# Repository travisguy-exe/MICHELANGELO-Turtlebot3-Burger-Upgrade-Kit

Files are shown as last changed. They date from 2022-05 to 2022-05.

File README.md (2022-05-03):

# MICHELANGLEO - Turtlebot3 (Burger) Upgrade Kit

**A 3D printable, open-source upgrade kit for the Turtlebot3 Burger from Robotis.**

 <span xmlns:dct="http://purl.org/dc/terms/" property="dct:title">The</span> <a xmlns:cc="http://creativecommons.org/ns#" href="https://github.com/travisguy-exe/MICHELANGELO-Turtlebot3-Burger-Upgrade-Kit" property="cc:attributionName" rel="cc:attributionURL">MICHELANGELO - Turtlebot3 Burger Upgrade Kit</a> by Travis Guy is licensed under a <a rel="license" href="http://creativecommons.org/licenses/by-nc-sa/4.0/">Creative Commons Attribution-NonCommercial-ShareAlike 4.0 International License</a>.

## **Kit Overview**

The Michelangelo upgrade kit is intended to increase the overall modularity and usability of the Turtlebot3 Burger platform. This is a valuable upgrade for anyone looking to improve the physical user friendliness, durability and modularity of their Turtlebot3 Burger unit. The following list outlines the key features of the Michelangelo Kit.



####  **Kit Features:**

- **Enclosures:** Fully 3D printable enclosures for both the Burger's **Raspberry Pi** and **OpenCR** boards, with solid mounting points.
- **Multi-Generation Support:** The MICHEALANGELO kit supports both the  Raspberry Pi 3B+ and the Raspberry Pi 4 versions of the Turtlebot3 Burger. This project repository contains unique Raspberry Pi enclosure models for both versions of the Burger.  
- **Solid LIDAR Mount:** A 3D printable solid mount for the LDS-01 LIDAR unit.
- **Improved User Experience**: The MICHELANGELO kit reimagines the construction of the Turtlebot3 burger making it easier to access key ports on the system's control boards. At the same time the  kit's reconstruction makes the robot easier to disassemble and customize.
- **Improved Modularity:** The MICHELANGELO upgrade kit adds modular enclosures and mounts to all of the key components of the Turtlbot3 Burger. This allows each of these components to easily be relocated, swapped out or customized as the user see's fit. CAD documentation for all models are included in this repository to allow users to create their own custom variants depending on their needs.

## **Repository Overview**

This repository contains all of the files and instructions necessary to upgrade a standard Turtlebot3 Burger unit with the MICHELANGELO kit. It as well contains all of the CAD documentation that one would require to add their own features to this upgrade kit. The following list provides detail on each of the sub-folders within this directory and where to locate relevant information within them.

**Repository Folders:**

- **3D Printing Files:** This folder contains all of the necessary **STL** files for printing the upgrade kit's parts, as well as, instruction for post processing.

- **CAD Files:** Contained within this folder are the **Fusion 360** and **.step** solid models for the MICHELANGELO Kit assembly and its sub-assemblies.

------

## **Project Log**

The MICHELANGELO project is still under active development, which means features will be added to this repository as time goes on! Refer back to this log to see what is upcoming and what I have added!

### Work In Progress.

- Youtube Assembly/Overview Video

### Completed Work

2022/04/30 - Project Inception

	- CAD Files - MICHELANGELO v44 Master Assemblies
	- Assembly Documentation
	- STL Files/3D Printing Documentation

------

## Bill of Materials

The following table outlines the items required to complete the MICHELANGELO upgrade:

| Item/Description | Qty. | |
| :--- | :---: | :---: |
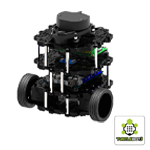
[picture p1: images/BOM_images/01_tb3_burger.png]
| Turtlebot 3 Burger Kit | 1 |   |
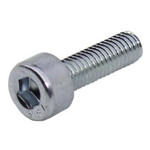
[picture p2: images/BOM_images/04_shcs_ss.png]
| **M3-0.5 x 6mm** - Socket Head Cap Screw - (42 Max.) | 12 (Min.) |  |
| **M3-0.5 x 16mm** - Socket Head Cap Screw | 12 |  |
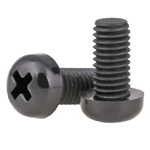
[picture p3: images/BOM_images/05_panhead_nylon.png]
| **M3-0.5 x 6mm** - Pan Head Screw (NYLON) | 8 |  |
| **M3-0.5 x 12mm** - Pan Head Screw (NYLON) | 2 |  |

# **Assembly Instructions**

	This section outlines the assembly instructions for the MICHELANGELO Upgrade Kit. These instructions assume that you have purchased all items in the **Bill of Materials** section and have 3D printed all relevant upgrade parts in accordance with the instructions laid out in the readme of the **3D Printing Files** folder.

------

### Step 1: TB3 Burger First Layer Assembly

------

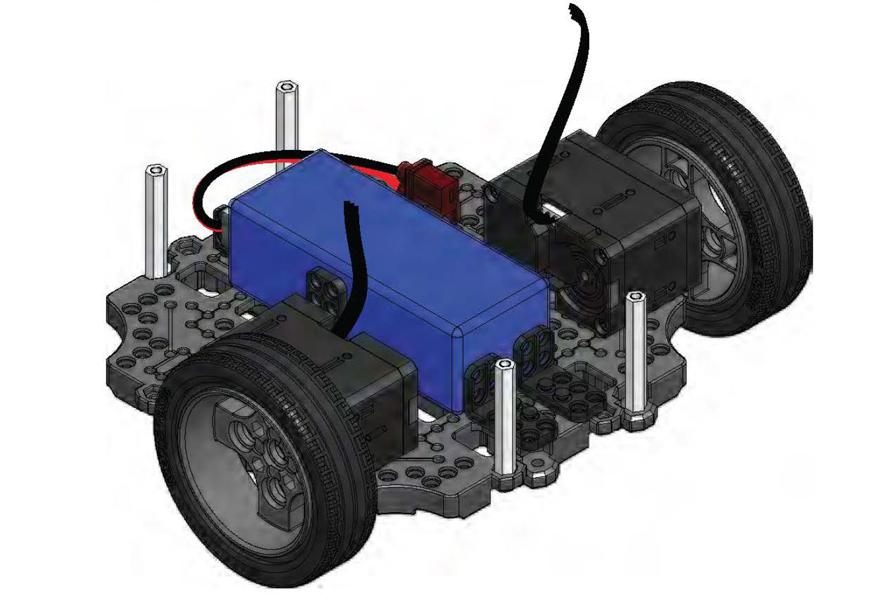
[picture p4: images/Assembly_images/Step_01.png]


The MICHELANGELO upgrade kit uses the **"First Layer Assembly"** from the standard Turtlebot3 Burger kit. Specific instructions for assembling the **"First Layer Assembly"** can be found on **Pages 11-15** of the Robotis Turtlebot3 Burger Assembly Manual. Once assembled, the **First Layer Assembly** can be set aside until **Step 4**

**Robotis Assembly Manual (Direct Download):** https://www.robotis.com/service/download.php?no=748

------

### Step 2: TB3 Burger Waffle Plate Assembly (x3)

------

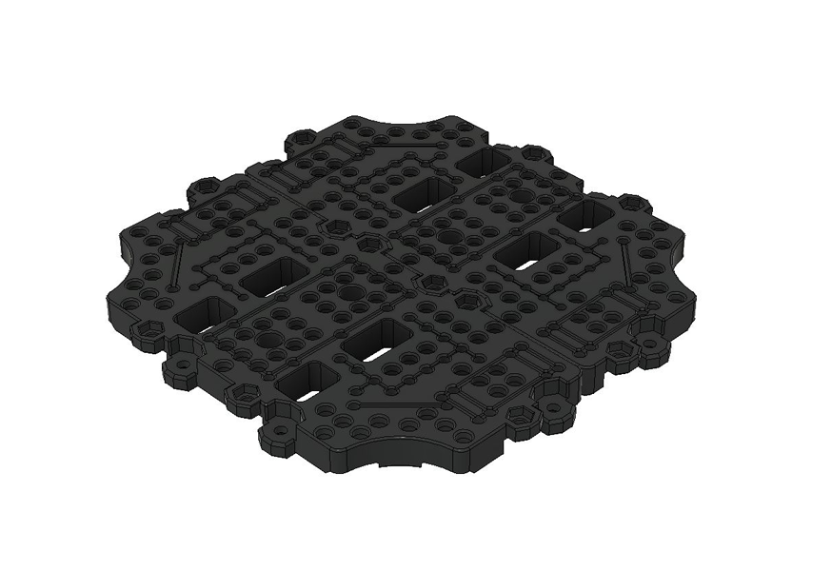
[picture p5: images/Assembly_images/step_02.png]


The MICHELANGELO kit uses the standard Burger waffle-plate assembly for all layers of the build. **Three** additional waffle-plates can be assembled at this point using the standard hardware from the Burger kit. These assembled waffle-plates can be set aside for later use in **Steps 3, 9 and 14**.

Instructions on **"Waffle-Plate Assembly"** can be found on **Page 9** of the Robotis Turtlebot3 Burger Assembly Manual. 

------

### Step 3: Second Layer Tap Locations ( OpenCR Enclosure Mounting)

------

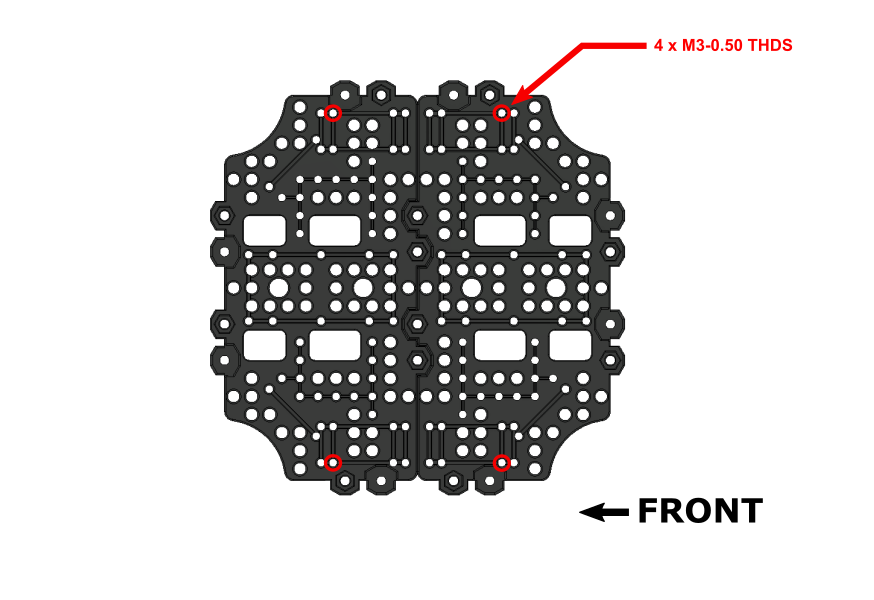
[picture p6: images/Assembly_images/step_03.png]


In order to attach the OpenCR board enclosure to a waffle-plate assembly, **4 pre-existing** holes must be modified. The image above indicates the relevant hole locations for tapping, an **M3-0.5** tap is required for this process. 

**NOTE:** Orientation of the second layer waffle-plate matters from this step onwards. Be sure to follow the orientation indicators for each subsequent step.

------

### Step 4: Second Layer Standoffs + OpenCR (Lower Enclosure) Installation

------

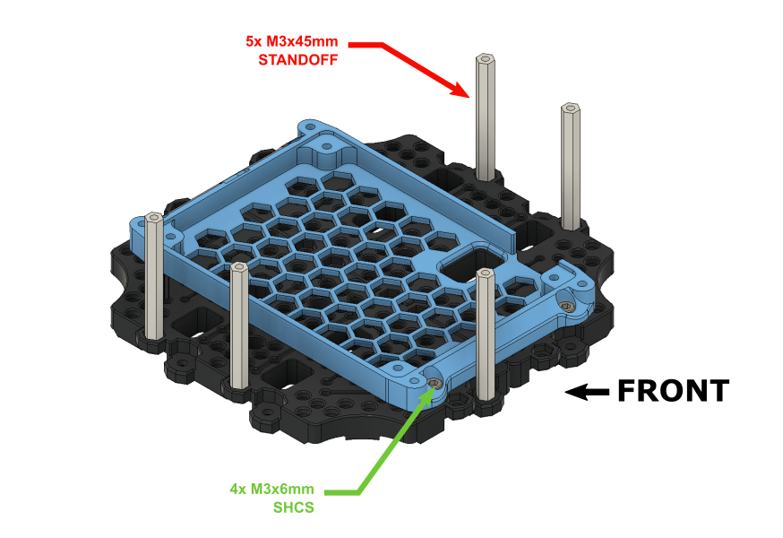
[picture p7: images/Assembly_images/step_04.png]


Attach the **OpenCR Lower Enclosure Half** to the **Second Layer Assembly** using **4 - M3x6mm Socket Screws**. Once the lower enclosure half is secured, install **5 - M3x45mm Standoffs** at the locations shown in the assembly image above. The standoffs can be attached with the standard **M3x8mm Philips** hardware from the Turtlbot3 Burger kit or an additional  **5 - M3x6mm Socket Screws**. 

------

### Step 5: Second Layer Attachment + Cable Routing

------

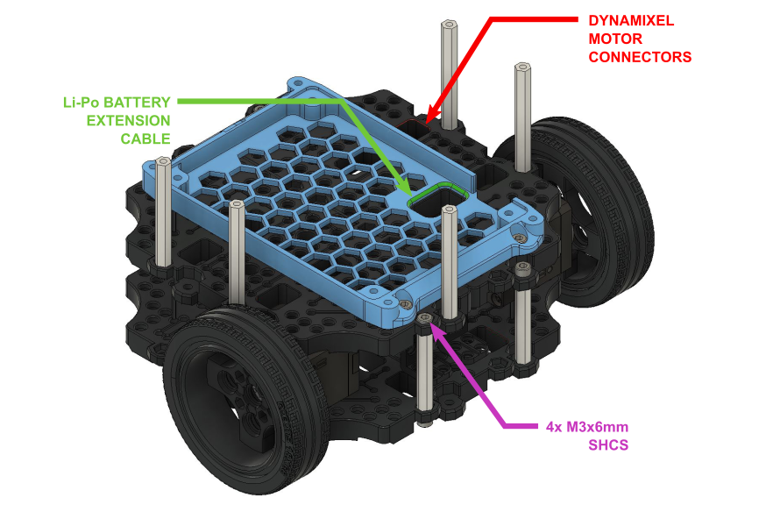
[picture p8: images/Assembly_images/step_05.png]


At this stage the **Second Layer Assembly** can be attached to the **First Layer Assembly** created in **Step 1**. However, before attachment, the **Dynamixel Motor Cables** and the **Li-Po Battery Extension Cable** from the first layer must be routed through the **Second Layer Assembly**. The image above shows the respective routing locations for each of the cables. 

A total of **4 - M3x6mm Socket Screws** screws are required to attach the second layer to the first. Alternatively, the standard **M3x8mm Philips**  hardware from the Turtlebot3 burger kit can be used in place of the socket screws. 

------

### Step 6: OpenCR Board Installation 

------

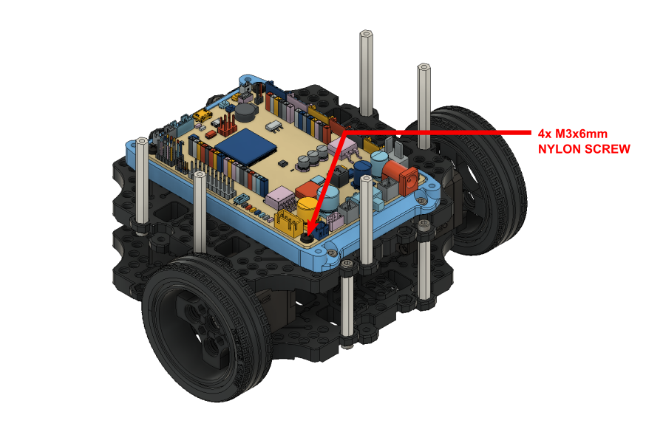
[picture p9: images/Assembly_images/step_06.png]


The **OpenCR** board  can now be installed into its lower enclosure half using **4 - M3x6mm Nylon Screws**. 

------

### Step 7: OpenCR Board Connections

------

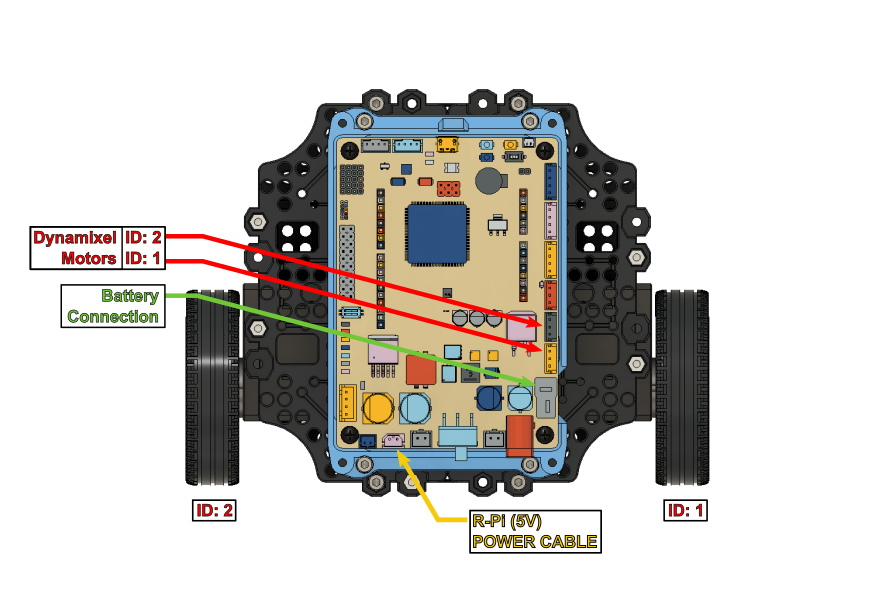
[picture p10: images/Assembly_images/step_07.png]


Before the OpenCR board can be fully enclosed a few electrical connections must be made: 

- [ ] Attach the **Dynamixel Motor** and **Li-Po Battery Extension** cables that were routed during **Step 5** to the OpenCR board. The connection points are indicated by the **RED** and **GREEN** arrowed text in the image above. 

  **NOTE:** Ensure correct connection of the Dynamixel motors by following the motor ID legend in the **RED** arrowed text. The motor IDs are indicated below each wheel for quick reference.

- [ ] Connect the **R-Pi (5v) Power Cable** to the OpenCR board at the point indicated by the **YELLOW** arrowed text in the image above. Leave this cable loose for routing in a later step.

------

### Step 8: OpenCR Enclosure Assembly

------

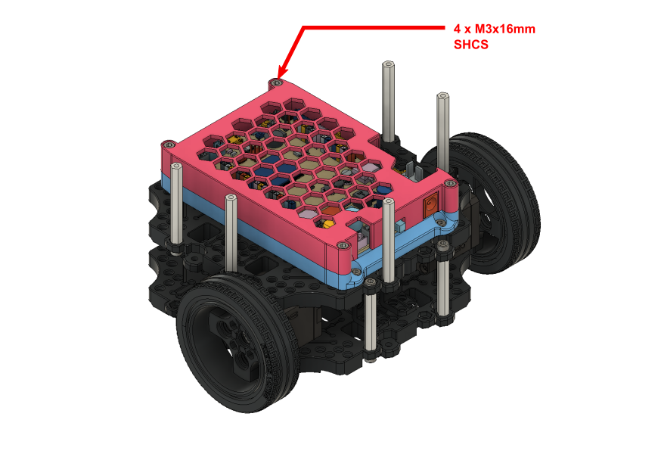
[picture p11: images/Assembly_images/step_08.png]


The OpenCR board can now be fully enclosed with it's upper enclosure half. As indicated in the assembly image above, a total of **4 - M3x16mm** fasteners will be required for this step.

------

### Step 9:  Third Layer Tap Locations (Raspberry Pi Enclosure Mounting)

------

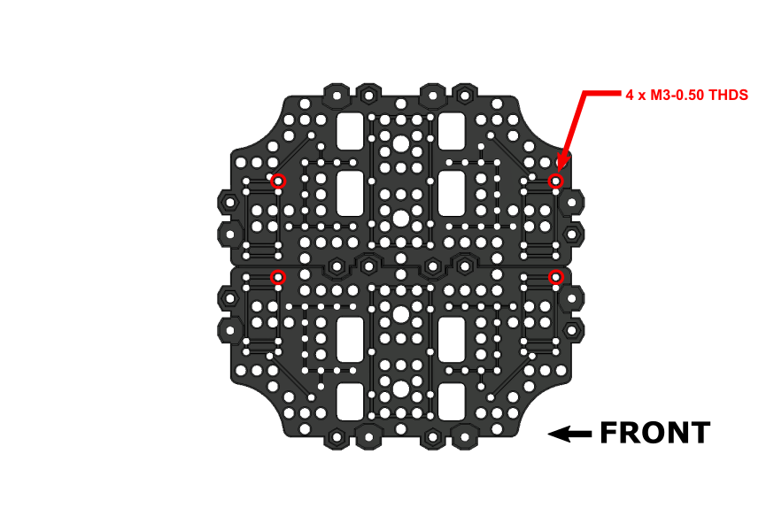
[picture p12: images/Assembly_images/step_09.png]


Whether you are using a **Raspberry Pi 3B+** or a **Raspberry Pi 4** the mounting footprint of theses enclosures in the MICHELANGELO upgrade kit are identical. These instructions apply for both models of the Turtlebot3 Burger.

In order to attach either Raspberry Pi board enclosure, **4 pre-existing** holes must be modified on the third layer waffle-plate. The **Step 3** image above indicates the relevant hole locations for tapping, an **M3-0.5** tap is required for this process. 

**NOTE:** Orientation of the third layer waffle-plate matters from this step onwards. Be sure to follow the orientation indicators for each subsequent step.

------

### Step 10:  Third Layer Standoffs + Raspberry Pi (Lower Enclosure) Installation

------

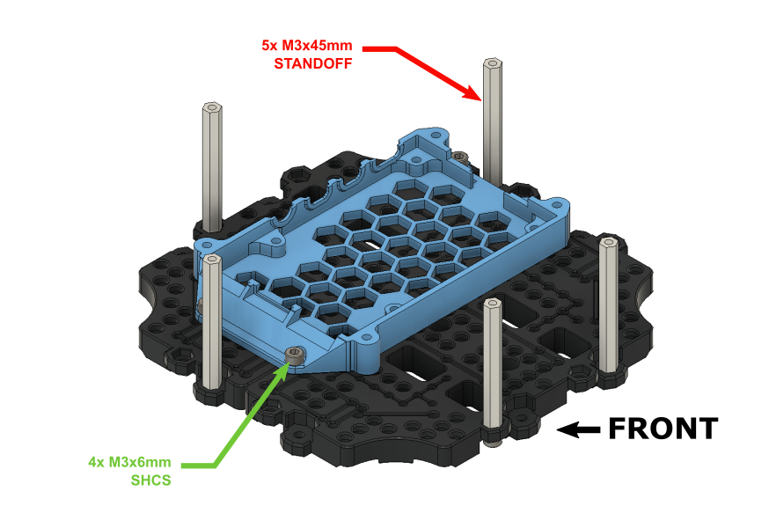
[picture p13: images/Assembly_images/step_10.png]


The **Raspberry Pi Lower Enclosure Half** can now be attached to the **Third Layer Assembly** using **4 - M3x6mm Socket Screws**. Once the lower enclosure half is secured, install **5 - M3x45mm Standoffs** at the locations shown in the assembly image above. The standoffs can be attached with the standard **M3x8mm Philips** hardware from the Turtlbot3 Burger kit or an additional  **5 - M3x6mm SHCS**. 

**NOTE:** This guide depicts the installation of the **Raspberry Pi 4** board. Instructions for the **Raspberry Pi 3B+** board are identical except for the usage of the relevant **3B+** enclosure pieces.

------

### Step 11:  Third Layer Attachment + Raspberry Pi Installation/Cable Routing

------

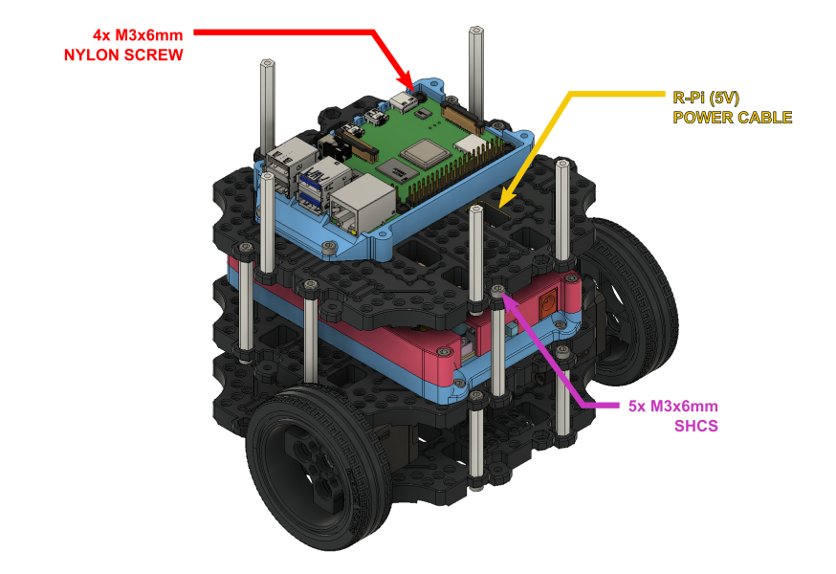
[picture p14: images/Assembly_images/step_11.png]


The **Third Layer Assembly** can now be attached to the main burger assembly using **5 - M3x6mm Socket Screws ** or the standard **M3x8mm Philips** hardware from the Burger kit. It is important that before fastening down the **Third Layer Assembly**, you first route the **R-Pi (5v) Power Cable** from **Step 7** up through the hole indicated by the **Yellow** arrowed text in the image above . 

Once the **Third Layer Assembly** is secured, install your Raspberry Pi unit into its mounted lower enclosure half using **4 - M3x6mm Nylon Screws**.

**NOTE:** Do not connect the **R-Pi (5v) Power Cable** during this step.

------

### Step 12:  Raspberry Pi Enclosure Assembly + Power Connection

------

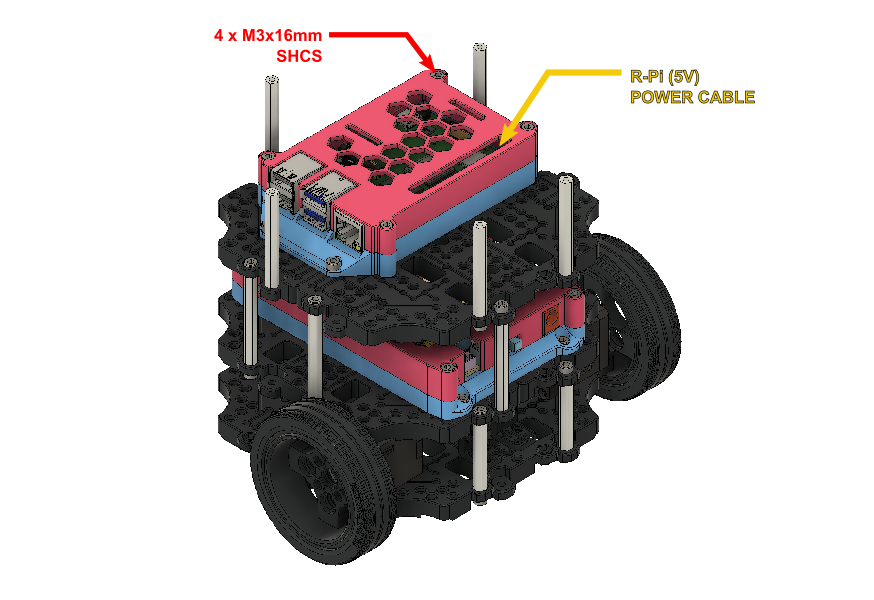
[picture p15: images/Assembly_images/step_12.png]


The Raspberry Pi board can now be fully enclosed with it's upper enclosure half, this step requires **4 - M3x16mm SHCS**.

Once the enclosure is assembled, connect the **R-Pi (5v) Power Cable** that was routed during **Step 11** to the Raspberry Pi unit.

**NOTE:** When connecting the power cable to the Raspberry Pi it is important to connect to the correct GPIO pins. Ensure that the **Positive** lead connects to **Pin 4** and the **Negative** lead connects to **Pin 6**. 

(Refer to **Page 22** of the Turtlebot3 Burger Assembly Manual for connection information.)

------

### Step 13:  Raspberry Pi - OpenCR USB Connection & Cable Routing

------

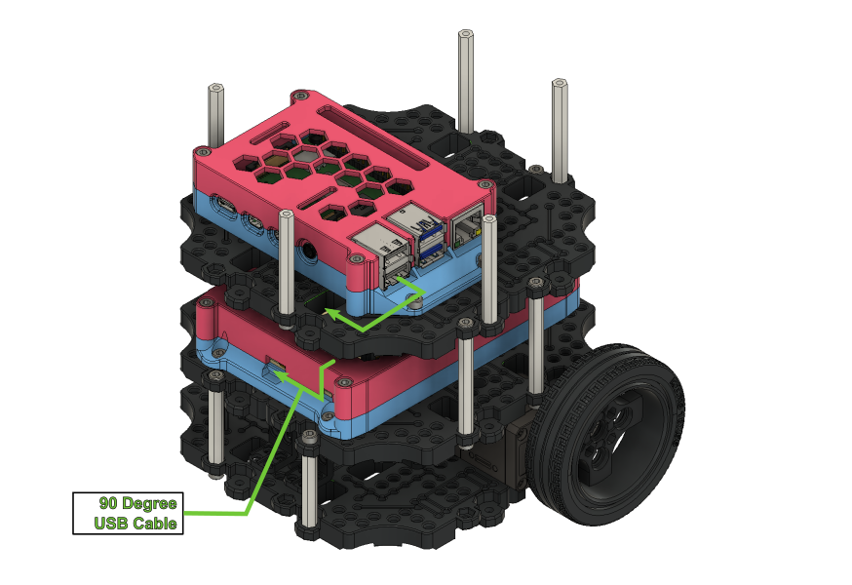
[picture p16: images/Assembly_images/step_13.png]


The USB connection between the **Raspberry Pi** and the **OpenCR** board can now be made using one of the **90 Degree USB Cables** from the Turtlebot3 Burger kit. The **Green** arrowed text in the image above shows the routing path for the USB cable, it can be routed down through the **Third Layer Assembly** waffle-plate to keep the connection tidy and tucked away.

------

### Step 14:  Fourth Layer Assembly and Tap Locations

------

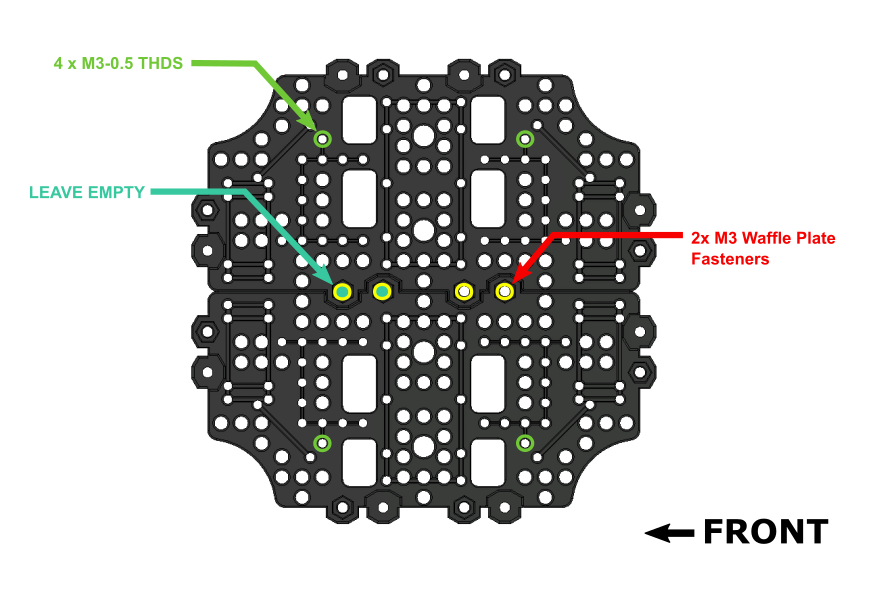
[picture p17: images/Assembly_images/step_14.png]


The **Fourth Layer Assembly** of the MICHELANGELO upgrade kit slightly alters the waffle-plate construction to allow mounting of the **USB2LDS** driver board on the underside of the layer. As indicated in the assembly image above it is important to leave the **LEFT** two waffle-plate fastener locations empty as they will be used in the next step.

Before proceeding to the next step a total of **4** pre-existing holes on the assembly must be tapped with an **M3-0.5** tap. These tapped holes are for attaching the the LDS-01 LIDAR mounting bracket. The **GREEN**  arrowed text in the image above indicates the relevant holes that require tapping.

 **NOTE:** Orientation of the fourth layer waffle-plate matters from this step onwards. Be sure to follow the orientation indicators for each subsequent step.

------

### Step 15:  USB2LDS Driver Board Installation

------

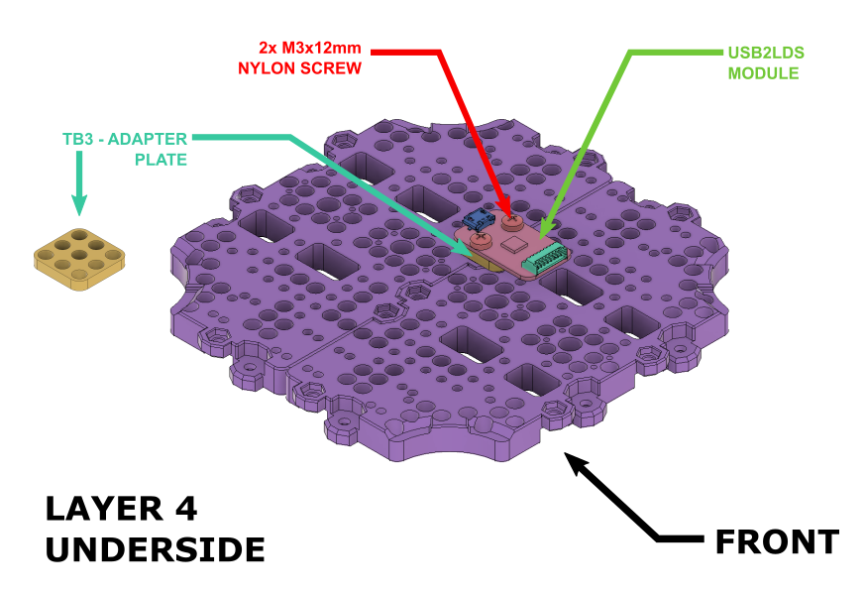
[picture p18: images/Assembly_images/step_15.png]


The **USB2LDS Module** from the Turtlebot3 kit can now be installed on the underside of the the **Fourth Layer Assembly**.  The module requires **2 - M3x12mm Nylon screws** that are fastened through the waffle-plate fastener locations left empty in **Step 14**. As indicated in the image above, the assembly also requires the **"Adapter Plate"** component from the Turtlebot3 kit, this component acts as a spacer for the module.

**NOTE:** The Nylon screws will protrude through the topside of the waffle plates. Use a pair of **flush-cut pliers** to trim the excess after the module has been tightly secured.

------

### Step 16:  LIDAR Mounting Bracket Installation

------

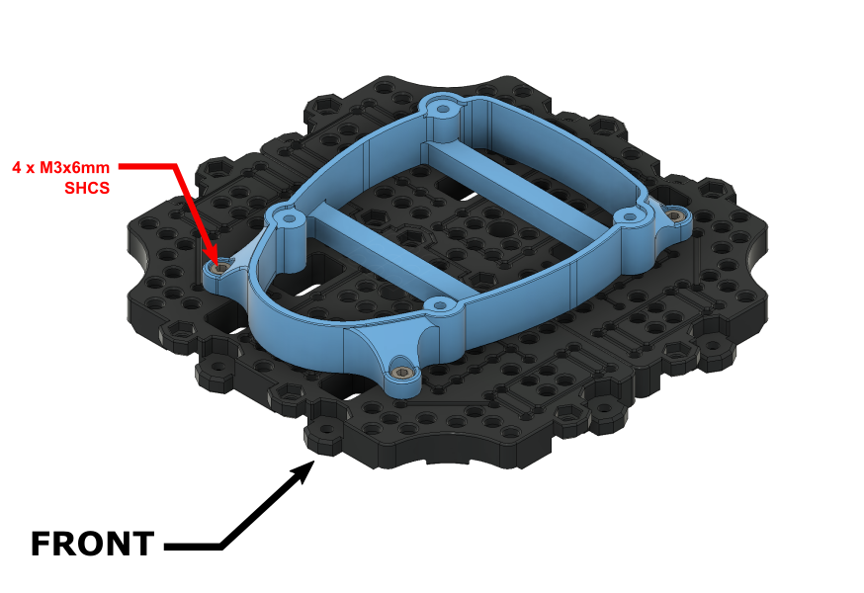
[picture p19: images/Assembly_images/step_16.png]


Turn the **Fourth Layer Assembly** back over and attach the LIDAR mounting bracket to the top side using **4 - M3x6mm Socket Screws**.  The LIDAR bracket's mounting position corresponds with the 4 tapped holes made previously in **Step 14**.

------

### Step 17: LDS-01 LIDAR Module Installation

------

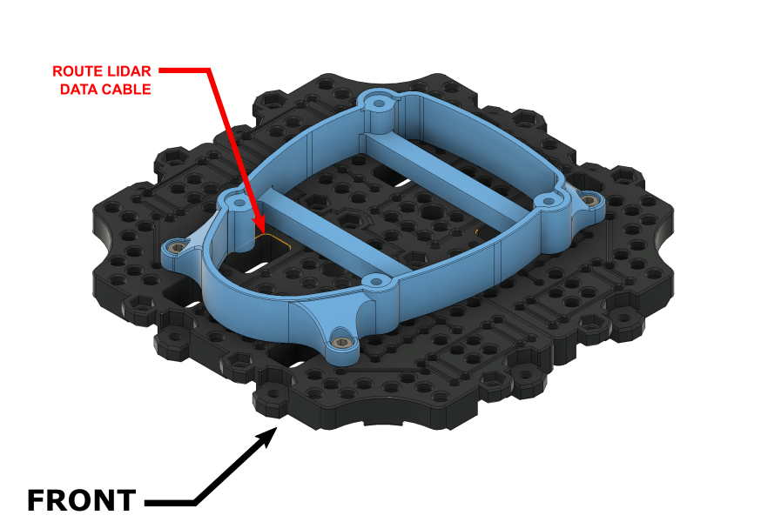
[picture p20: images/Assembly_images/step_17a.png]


------

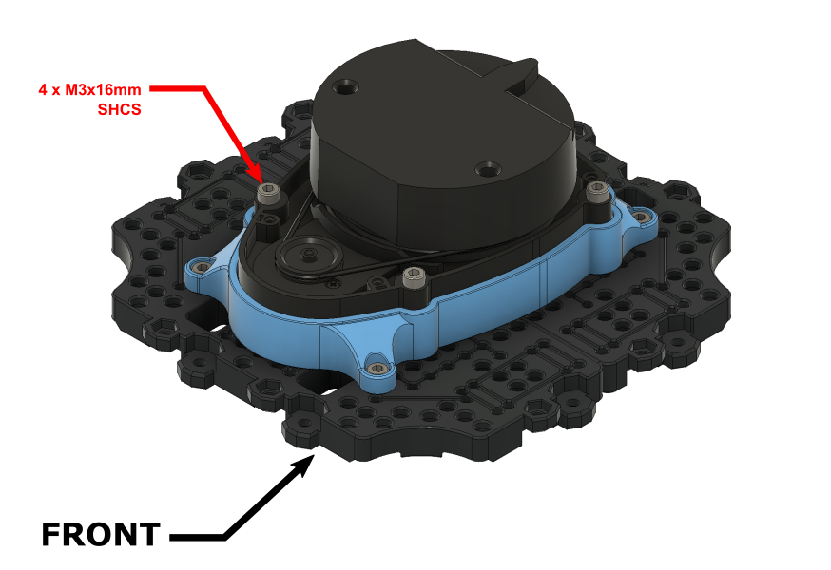
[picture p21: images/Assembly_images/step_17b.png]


**NOTE:** Before Mounting the **LDS-01 LIDAR** unit's mounting holes will have to be modified to accept M3 sized fasteners. Drill out the unit's 4 outer mounting holes using a 3.15mm or (1/8") drill bit.

Attach the **LDS-01 LIDAR** unit from the Turltbot3 kit to the mounting bracket using **4 - M3x16mm Socket Screws**. Be sure to route the unit's data cable though the opening highlighted in **YELLOW** before fastening. Once fastened make sure to connect the **LDS-01 LIDAR** data cable to the **USB2LDS Module** on the underside of the layer.

------

### Step 18:  Fourth Layer Attachment + Raspberry Pi - USB2LDS Connection

------

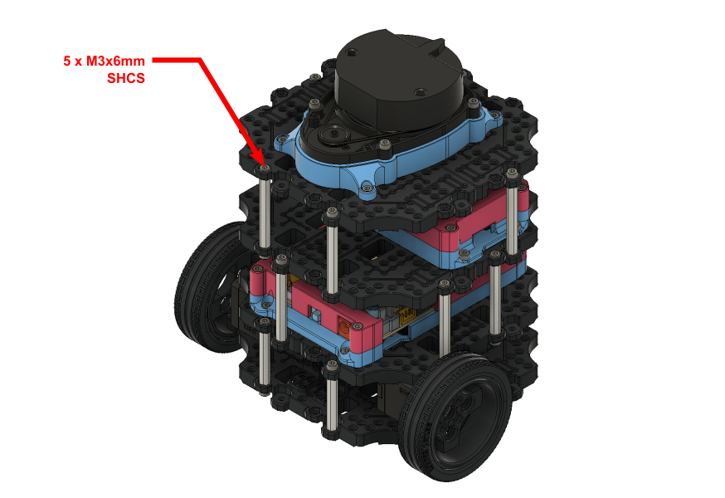
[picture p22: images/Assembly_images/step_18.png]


The **Fourth Layer Assembly** can now be attached to the main assembly using either **5 - M3x6mm Socket Screws ** or the standard **M3x8mm Philips** hardware from the Burger kit. 

**NOTE:**  Before fastening down the **Fourth Layer Assembly**, be sure to connect the **Raspberry Pi** to the **USB2LDS Driver Board** using the remaining 90 Degree USB cable from the Turtlebot3 Burger kit.

Once these steps are complete, your Turtlebot3 Burger is ready to use. Congratulations on upgrading your Burger with the MICHELANGELO kit!

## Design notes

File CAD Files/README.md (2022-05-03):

# **MICHELANGELO - CAD FILES - (v44)**

This folder contains the master assembly file for the MICHELANGELO mod kit, it is available in 2 different formats (**.f3z** & **.step**). The image below depicts the contents of the assembly files.

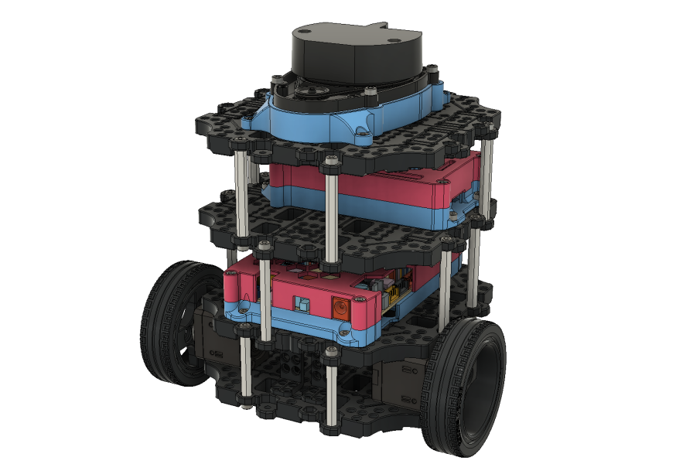
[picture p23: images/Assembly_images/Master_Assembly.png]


The MICHELANGELO mod kit was developed in **Fusion 360**, if this is your native CAD program I recommend downloading the **.f3z** format of the master assembly. This will provide you with the master assembly and all of the individual linked sub-assemblies. The .f3z file also contains captured design history of each part, for ease of personal modification. 

If you are **not** a **Fusion 360** user, you can still download the neutral format of the master assembly (**.step**). This variant, however, exists as single standalone assembly and does not contain any of the captured design history.

**Special License Considerations & Credits:**

[1] - The sub-assembly "RPi Case - Assembly" was based upon the work of Thingiverse user "[0110-M-P](https://www.thingiverse.com/0110-M-P)" and is licensed as follows:

 <span xmlns:dct="http://purl.org/dc/terms/" property="dct:title">RPi Case - Assembly</span> by <a xmlns:cc="http://creativecommons.org/ns#" href="https://github.com/travisguy-exe/LEONARDO-turtlebot3-wafflepi-upgrade-kit" property="cc:attributionName" rel="cc:attributionURL">Travis Guy</a> is licensed under a <a rel="license" href="http://creativecommons.org/licenses/by-sa/4.0/">Creative Commons Attribution-ShareAlike 4.0 International License</a>. Based on a work at <a xmlns:dct="http://purl.org/dc/terms/" href="https://www.thingiverse.com/thing:922740" rel="dct:source">https://www.thingiverse.com/thing:922740</a>.

[2] - The standard CAD assets of the Turtlebot3 Waffle Pi unit were obtained from Robotis, and can be found at the following link:

https://cad.onshape.com/documents/179d4ba2a1f9231f93cae6e2/w/71e9066aee42d5039f880e2f/e/3cb7d487c93655e7067a3d5f

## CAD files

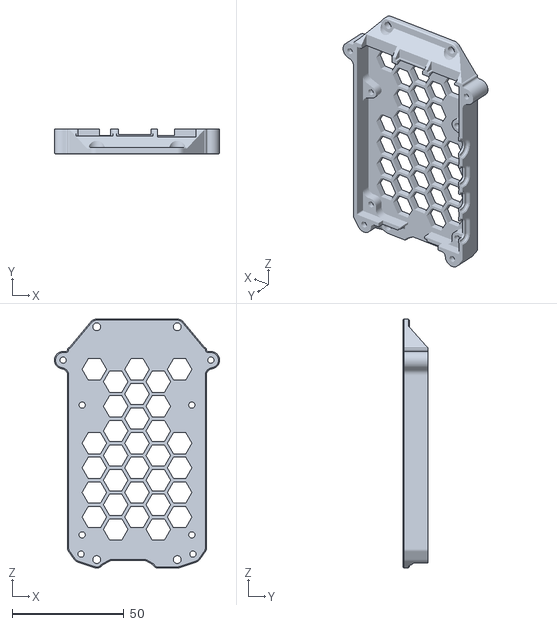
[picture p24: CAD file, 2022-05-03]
3D Printing Files/04a - RPi 4B Case Burger (Lower) - v8.stl
73.8 x 11.3 x 111.2

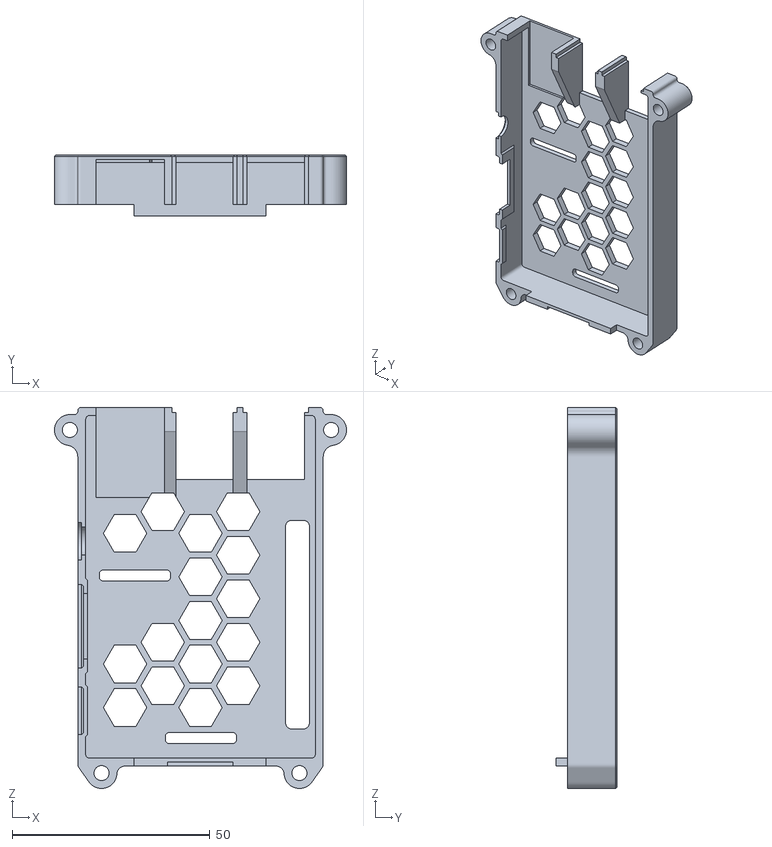
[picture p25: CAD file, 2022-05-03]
3D Printing Files/05b - RPi 3B+ Case Burger (Upper) - v15.stl
73.8 x 15.5 x 96.2

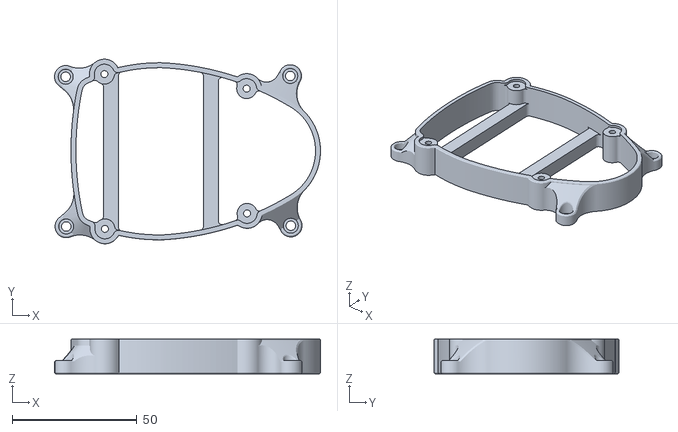
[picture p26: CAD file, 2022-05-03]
3D Printing Files/01 - LIDAR Mounting Bracket Burger - v6.stl
106.6 x 74.0 x 14.0

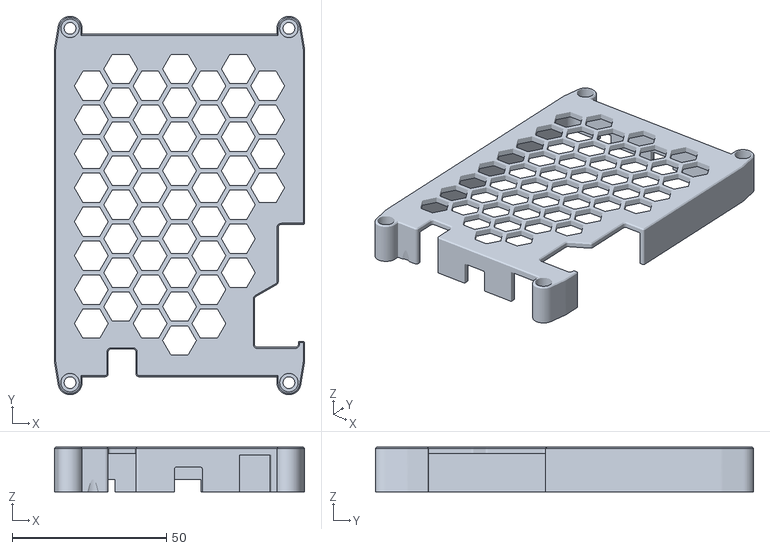
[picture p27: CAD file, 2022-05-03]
3D Printing Files/03 - OpenCR Case Burger (Upper) - v19.stl
81.0 x 122.6 x 14.5

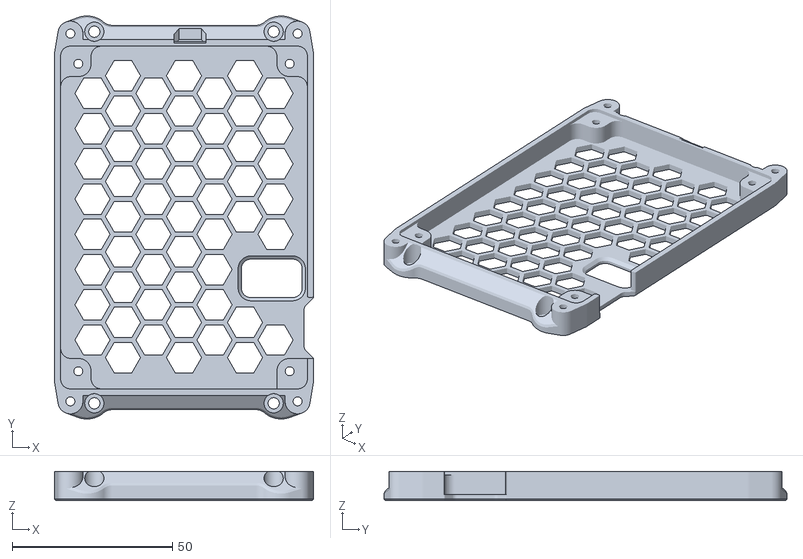
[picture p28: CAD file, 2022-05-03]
3D Printing Files/02 - OpenCR Case Burger (Lower) - v19.stl
81.0 x 125.8 x 9.20

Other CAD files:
3D Printing Files/05a - RPi 4B Case Burger (Upper) - v8.stl
3D Printing Files/04b - RPi 3B+ Case Burger (Lower) - v15.stl

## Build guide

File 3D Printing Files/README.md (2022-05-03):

## 3D Printing/Post Processing Instructions

The MICHELANGELO upgrade kit requires **1** print of each part contained within this sub folder. The parts have been designed to be easily printable on any FDM type printer. 

**NOTE:** This folder contains Raspberry Pi enclosure variants for both the **Raspberry Pi 3B+** and the newer **Raspberry Pi 4**. Print the case relevant to your version of the Turtlebot3 Burger.

Once printed, several holes on Parts No. **01**, **02**, and **04** require **tapping**. An **M3-0.5** tap is required for this process. The **RED** circles in the image below indicate the relevant holes that require tapping on each part.

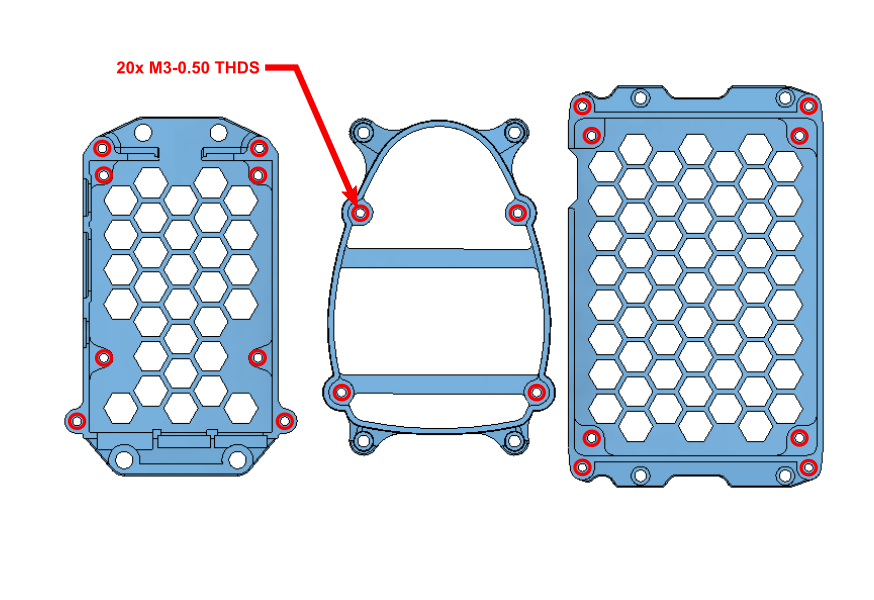
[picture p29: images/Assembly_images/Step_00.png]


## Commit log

2022-05-03 CAD File Upload - MICHELANGELO V44
2022-05-03 STL File Upload
    [01 - LIDAR Mounting Bracket Burger - v6.stl, 02 - OpenCR Case Burger (Lower) - v19.stl, 03 - OpenCR Case Burger (Upper) - v19.stl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]
